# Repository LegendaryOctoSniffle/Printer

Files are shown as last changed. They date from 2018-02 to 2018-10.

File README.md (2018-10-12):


# Printer

Design is complete. It works:

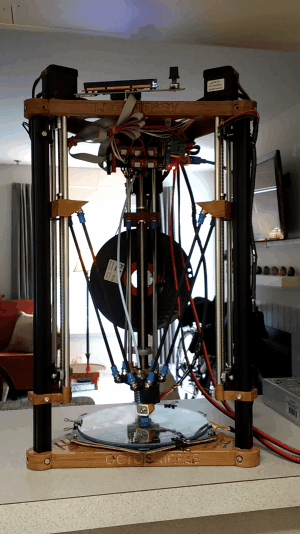
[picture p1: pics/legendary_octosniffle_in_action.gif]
the legendary octosniffle in action


This repository is for the LegendaryOctoSniffle design group. The LegendaryOctoSniffle will be a new 3D delta printer design, inspired by the RepRap [Kossel](http://reprap.org/wiki/Kossel) and [3DR](http://reprap.org/wiki/3DR). The printer will be designed around lead-screw drives and magnetic effector joints.

This repository will ultimately include models, images, instructions, parts lists, etc., for the construction of the LegendaryOctoSniffle. Presently, it contains coordinating instructions for the design group who will be creating these materials.

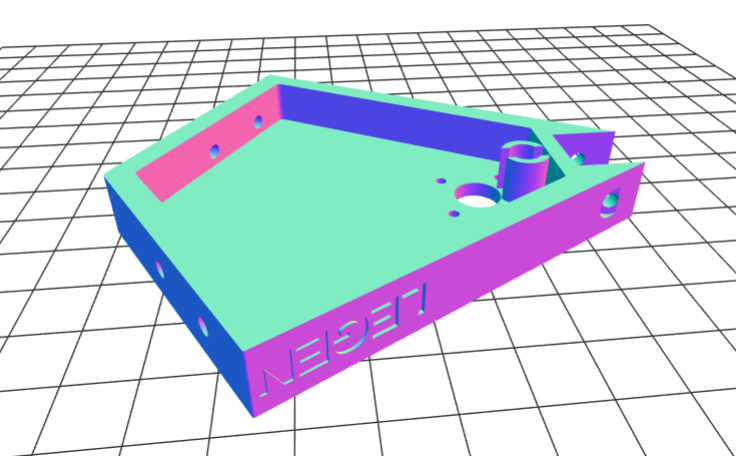
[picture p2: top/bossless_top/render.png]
Bossless top


## Goals

The primary design goals will be simplicity of assembly and simplicity of design: the LegendaryOctoSniffle will include a 3D printed structural top and base (inspired by the 3DR), magnetic effector joints, and a lead-screw drive. Aside from waiting for glue to dry, a practiced individual should be able to assemble the LegendaryOctoSniffle in one hour; a novice should be able to assemble it in less than four hours.

A secondary goal of the LegendaryOctoSniffle is to be a [RepRap machine](http://reprap.org/wiki/RepRap_Machines), like the Kossel, 3DR, and other machines that it is inspired by. The main requirement for this goal will be the licensing restrictions of any parts that the design group borrows from: GPL licensed parts will certainly be compatible with the RepRap project, and other licenses may also be suitable.

Another secondary goal of the printer is that it should be inexpensive. The basic build cost will be under $300.

## Audience

This repository currently supports the people who are designing the printer. It is anarchic, chaotic, and informal!

At some point, this repository might become a kind of reproducible design/learning experience for designing your own 3D printer.

## Structure

We will meet once a month for 4 or 5 months. The basic structure will be:

1. We'll buy some parts for the upcoming meeting.
2. We'll explore the function of those parts.
3. (Optional) We'll design the 3D printed parts necessary to assemble your purchased parts together. You can contribute to the design of these parts or just use other people's designs. Multiple people can independently design their own parts, working alone or together with others. And in the end, we don't have to settle on one "final" design: different people can use different solutions that they like best. Additionally, some parts can be taken directly from existing designs on the internet.
4. Send me your designs a week before the next meeting, and I'll have them printed for you. Or you can print them on your own if you have access to a 3D printer through a library, or work, etc.

## Schedule

### [Meeting 01: March 11th, 1:00PM, Study Room 5, Foster Business Library, University of Washington](meeting-01/)
### [Meeting 02: April 8th, 1:00PM-3:00PM, Suzallo Library Room 334, University of Washington](meeting-02/)
### [Meeting 03: July 7th. 1:00PM-3:00PM. University of Washington Campus (Suzallo 333)](meeting-03/)
### [Meeting 04: August 4th. 1:00PM-4:00PM. Radius Apartments rooftop common area (400 Boren Ave N, Seattle--SLU)](meeting-04/)

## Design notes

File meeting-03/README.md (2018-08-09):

# Meeting 03 - Saturday, July 7th. 1PM-3PM. University of Washington Campus (Suzzallo 333)

In this meeting, we will finish off the *structural* elements of our printer. In our next (and final) meeting, we will complete the *electrical* components of our printer.

## Parts

Here are the parts that you will need to purchase:

* 2020 Aluminum Extrusion (600mm) (x1)
  Yes, just one! [Ebay](https://www.ebay.com/itm/322880737350)
* T8x2 Leadscrew w/nut (500mm) (x2)
  Last time you bought 400mm. This time, buy two of the *500mm*. I'll swap you in third 500mm lead screw. Make sure that they are T8x2 screws. [Ebay](https://www.ebay.com/itm/322001200138?var=510950737978)
* Stepper Motor (Nema17, 1.7A) (x3)
  You have already bought one of these. Buy three more. You'll need two for the other two legs, and one for the extruder: the motor that pushes filament through the print head. [Ebay](https://www.ebay.com/itm/321966121485)
  
The quantities are weird because I'm making a shorter printer to fit on my counter, and I'll be giving you some of my longer parts. If you've already bought all three of your 2020 extrusions and lead screws, then that's not a problem!

## Pics from 7/7 meeting

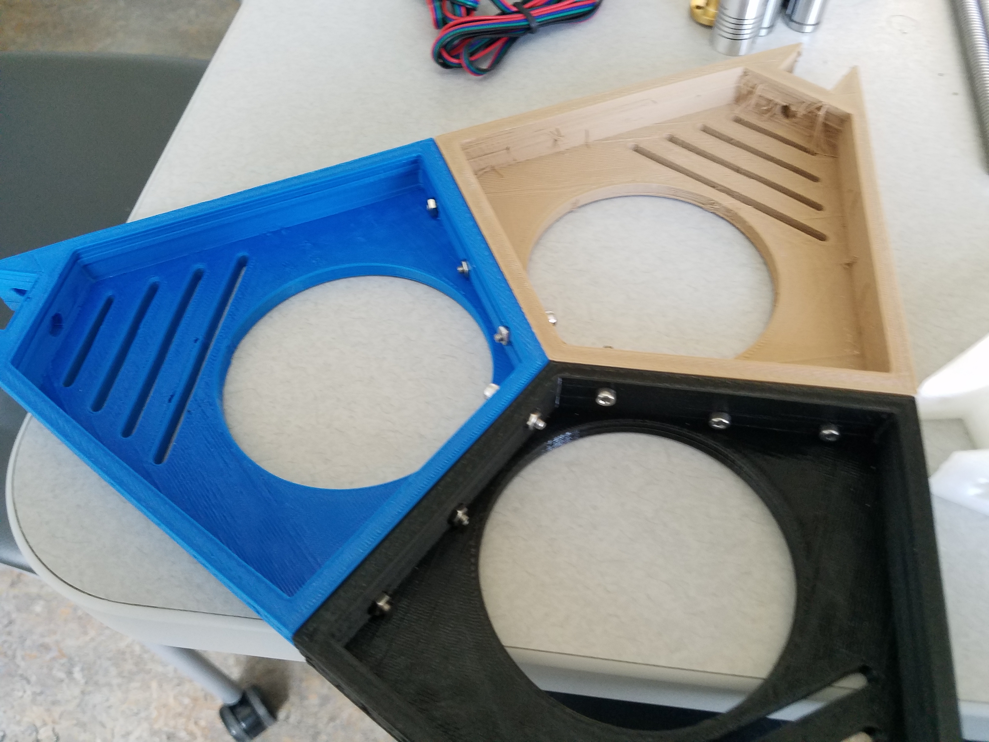
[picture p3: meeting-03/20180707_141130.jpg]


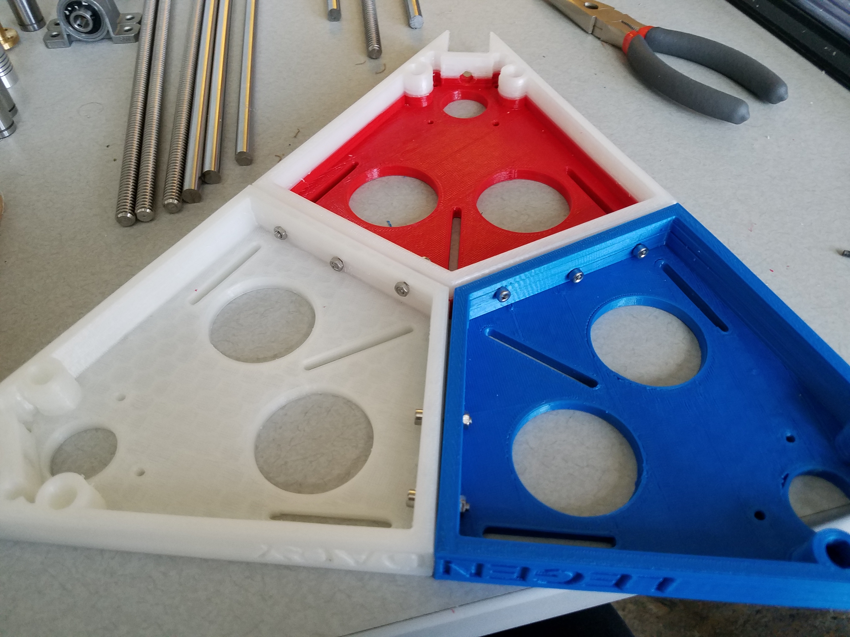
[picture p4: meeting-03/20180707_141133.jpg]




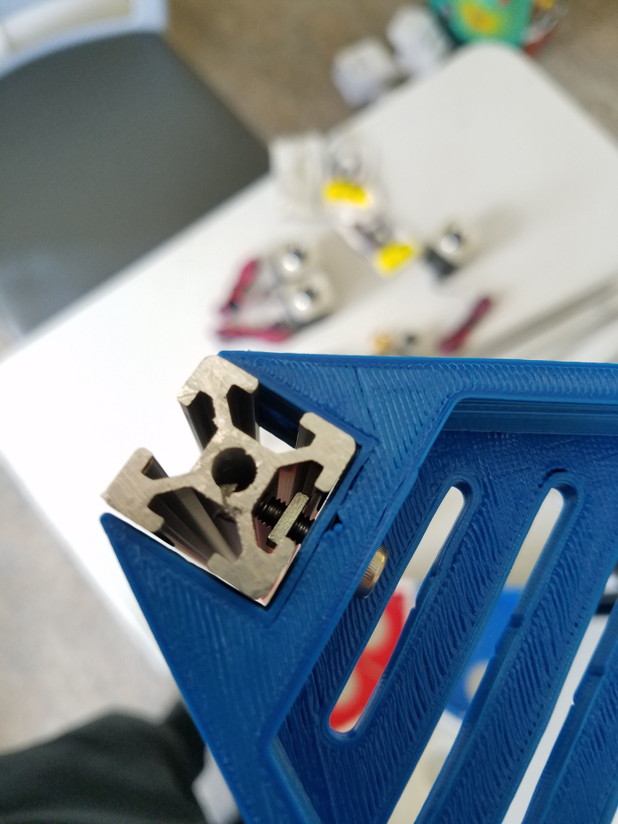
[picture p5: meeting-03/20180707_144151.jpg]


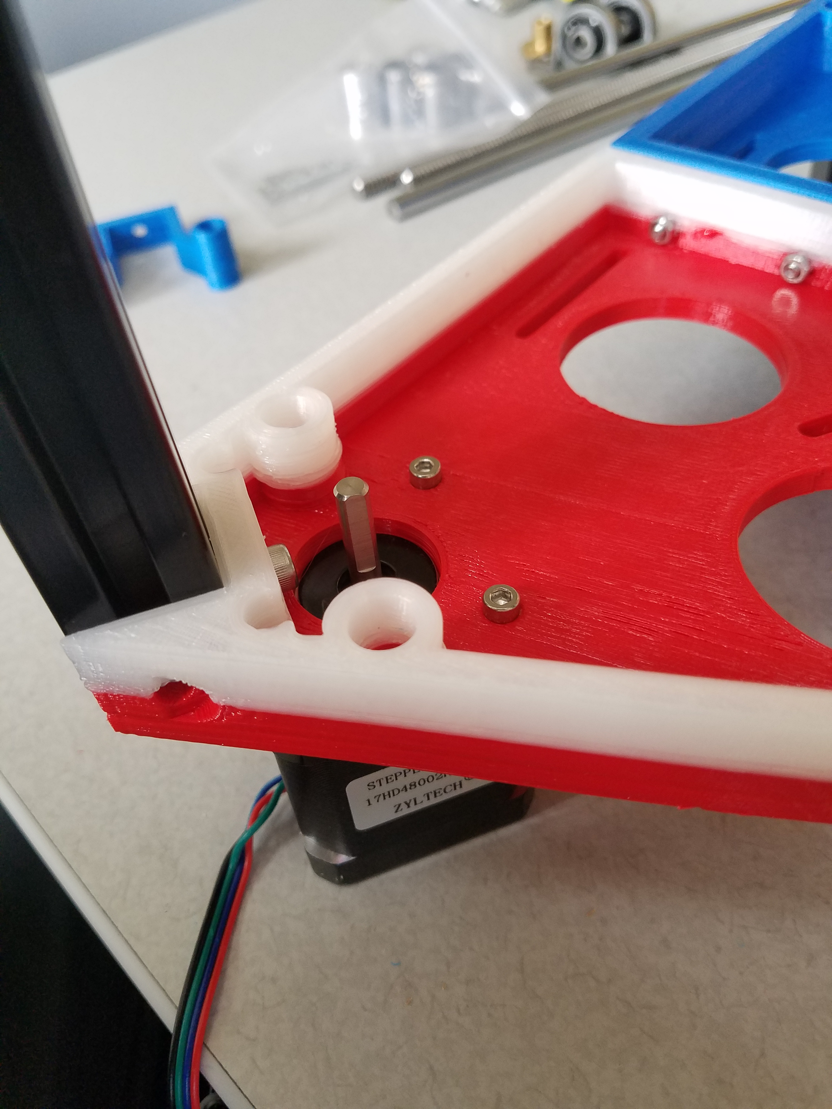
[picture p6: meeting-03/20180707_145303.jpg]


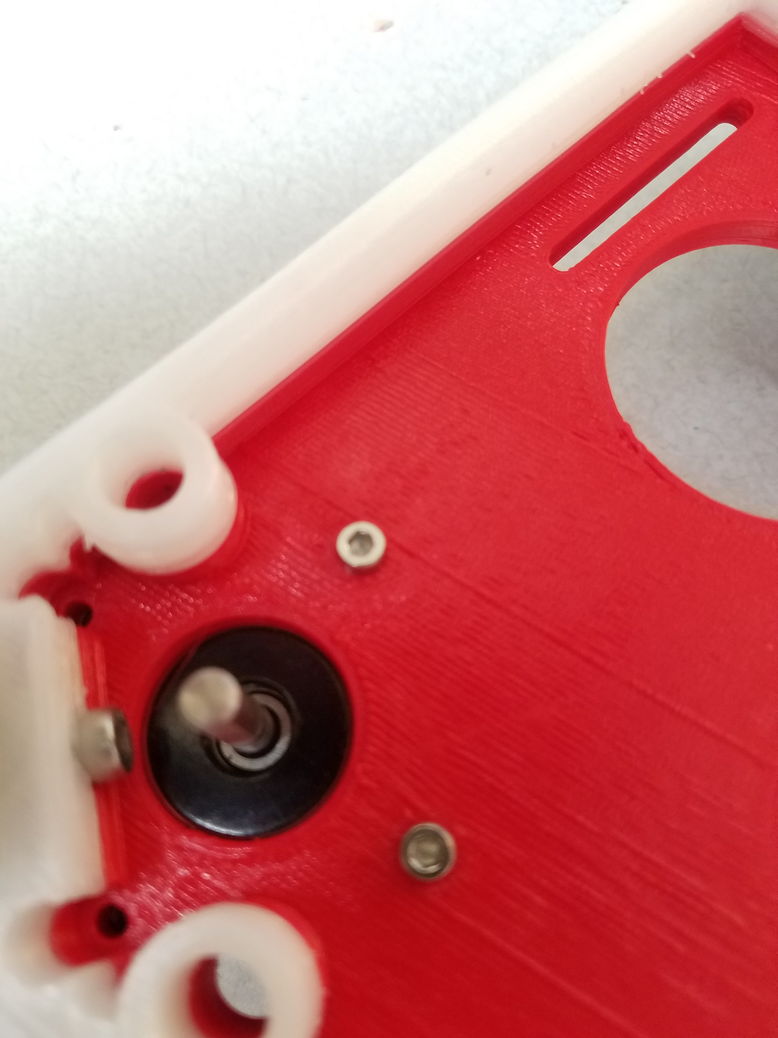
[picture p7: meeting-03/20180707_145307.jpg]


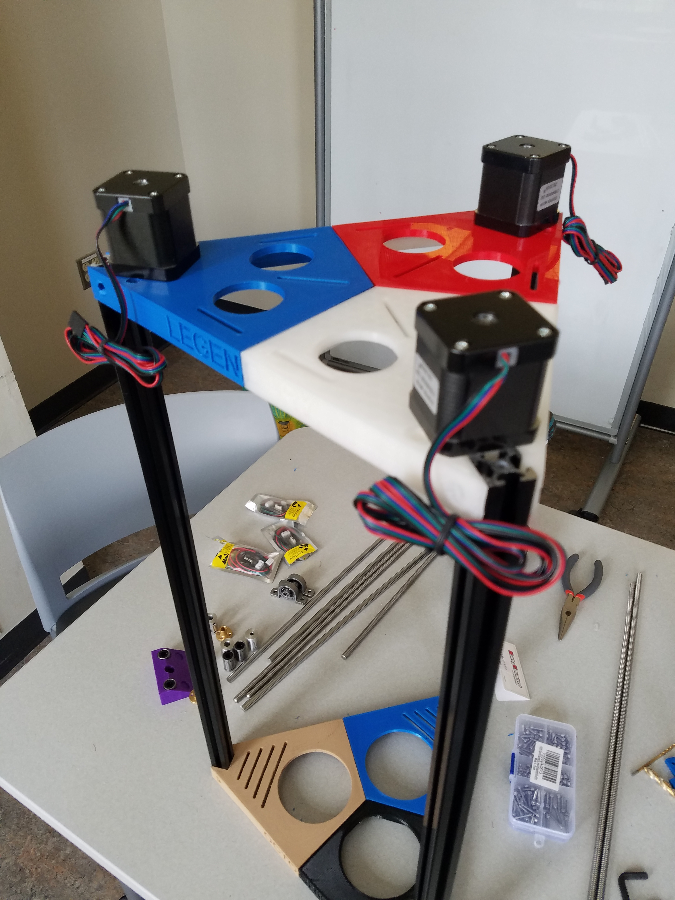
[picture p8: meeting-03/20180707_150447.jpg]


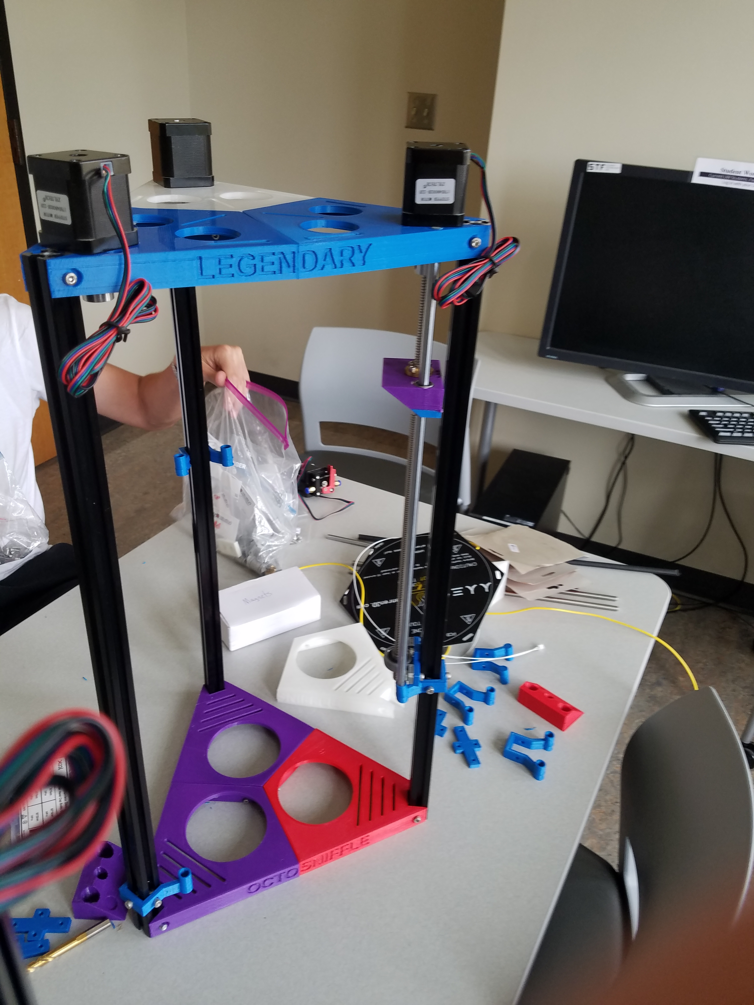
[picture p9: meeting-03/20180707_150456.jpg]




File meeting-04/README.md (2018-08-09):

# Meeting 04 - Saturday, August 4th. 1PM-4PM. Radius Apartments (Mike's building) __[rooftop common area](http://www.radiusslu.com/gallery/level-eight-amenities/)__: 400 Boren Ave N, Seattle, WA 98109 (South Lake Union) __[Map](https://goo.gl/maps/6jpcmqKH3d52)__

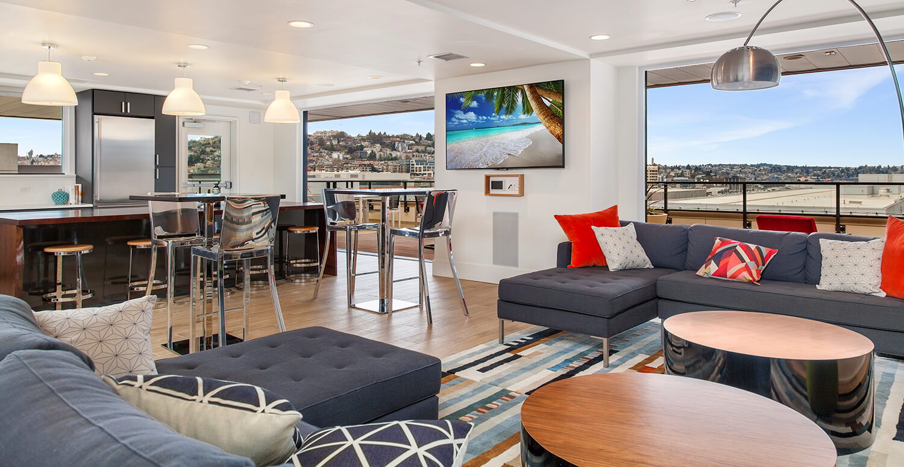
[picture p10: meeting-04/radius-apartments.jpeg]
Radius Apartments common area


In this (final) meeting, we will complete the *electrical* components of our printer. We're likely to use up all three hours calibrating our printers.

## Parts

* Power supply! 30 amps will be enough for a heated bed, plus dual extrusion (print two colors) if you decide to upgrade later. [Ebay](https://www.ebay.com/itm/Zyltech-12V-30A-360W-power-supply-PSU-for-3D-Printer-CNC-Arduino-Reprap-etc/322100961991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)
* Filament. Take your pick from [zyltech](https://www.ebay.com/sch/m.html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) on Ebay or on [Amazon](https://smile.amazon.com/s/ref=nb_sb_noss_2?url=search-alias%3Daps&field-keywords=PLA+1.75+filament). Get your color of choice, and anything with a decent rating will do. Don't get a specialty wood, metal, or fibre filament. It's important to get 1.75mm PLA. Get a full kilogram. Polylactic Acid (PLA) is plant-based, it has a fairly low melting temperature, and it doesn't shrink much as it cools.
* Control board! The RepRap Arduino Mega Pololu Shield (RAMPS) controller is based on an Arduino Mega 2560, with a 3D printer controlling "shield". Basically, we load a program onto the Arduino that has all of the logic of controlling the printer, and the Arduino talks to a second card which has all of the hardware for interfacing with the motors and heating elements. [ebay](https://www.ebay.com/itm/RAMPS-1-4-3D-PRINTER-CONTROLLER-Mega-2560-Atmega16u2-5x-A4988-2A-Drivers-More/321974766842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)
* LCD Controller. This LCD display includes an SD card reader and a wheel/button that lets you control the printer without attacking your computer. [ebay](https://www.ebay.com/itm/RAMPS-1-4-3D-PRINTER-2004-LCD-Smart-Controller/322017450535) Or if you wanted to be really cool, you could spring for this high(er) definition LCD: [ebay](https://www.ebay.com/itm/Genuine-ZYLtech-RAMPS-1-4-3D-PRINTER-12864-LCD-smart-controller/322148400468)
* Hot end. This is the part that we heat up and push plastic through. There are several manufacturers of hot ends, but most of them make clones of E3D. The V6 is E3D's flagship hot end, and so most manufacturers clone that version. Consequently, most printers are designed to accomodate a "V6 style" hotend. As simple as they are, hotends are somewhat prone to failure, and so it's worth it to spend a few extra dollars to get a decent one. For our printer, we will also need a "Bowden" style setup, which refers to separating the hotend of the extruder from the motor that is pushing filament through it. I'd suggest buying from Zyltech. [ebay](https://www.ebay.com/itm/V6-Style-Hotend-1-75mm-Bowden-style-Extruder-Conversion-Kit/322658052164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)
* Cold end. The "cold end" of the extruder is the part that pushes the plastic filament into the hot end. Here is a suitable one: [ebay](https://www.ebay.com/itm/2017-MK8-All-metal-1-75mm-Remote-Extruder-Kit-For-3D-Printer-Makerbot-Reprap-EV/222577699638). Either the "right" or "left" direction is fine.
* Build plate. The printer has to print "on" to a surface. Although it's not strictly necessary, an ideal build plate is heated to help keep the print warm through the duration of the entire print: this helps keep it from warping. Delta printers use round build plates. I would recommend buying [this](http://a.co/3r2tx1Q) one: people have knocked off stars for various reasons, none of which actually matter too much for our printer.

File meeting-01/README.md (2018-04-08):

Thanks to Kayla 🤘 for taking pictures and video, throughout Joe's explanations on how we'll be constructing 🏗️ the printer legs.

# Meeting 01

#### [See pics/vid from this meetup](https://github.com/LegendaryOctoSniffle/Printer/tree/master/meeting-01)

## Before the Meeting

Go ahead and purchase your [initial parts for meeting 01](#parts). I've received mine, and I'm excited! You might not have to bring all of your parts every time, but for this one do bring all of the parts that you receive. I received mine within a week of my order, but if you haven't received all of them by March 11th it won't be a big problem.

I'll refer to [this video](https://youtu.be/KroO4_xwKcs) to explain some of the parts that we'll be buying. Some of the parts and mechanisms will be different, but the basics will be the same.

The goal for the first meeting will be to create a working sled drive, minus the 3D printed parts. In the video above, the sleds are the orange things moving up and down the square rails.

The printer in the video uses a belt drive: the sleds are attached to a belt which is turned by motors in the base of the printer. The printer that we're making won't be using a belt: it will use a heavy threaded rod that's specially designed for driving precision movements.

## Parts

For our first meeting, we'll be assembling one "leg" of our printer. Though the parts list below is sufficient for one leg of the printer, we'll eventually be ordering three of all of the quantities provided below.

* T8x2 Leadscrew w/nut (400mm) (x1)
  This will be the threaded rod that will move each of our sleds up and down. We'll couple the motor to one end, and secure the length of the rod with a bearing that lets it turn freely. The x2 doesn't mean to buy 2 (yet), it designates the number of threads on the rod. [Ebay](https://www.ebay.com/itm/322001200138?var=510932183194)
* 8mm pillow block bearing. (x2)
  These are the bearings that will keep the rod aligned in place while letting it turn freely. Buy two. [Ebay](https://www.ebay.com/itm/2X-8mm-pillow-block-Self-aligning-bearing-mounted-support-3D-printer-CNC-Reprap-/322008974125). The linked item is a 2 pack: you can buy just one two pack. [Alternate Ebay listing](https://www.ebay.com/itm/2pcs-KP08-P08-8mm-Diameter-Bore-Self-Aligning-Pillow-Block-Bearing-/132306260310): if the first listing sells out, you can buy also buy this from the seller of the LM8UU bearings.
* 2020 Aluminum Extrusion (600mm) (x1)
  A mainstay of 3D printer construction. You'll see why. We'll use these as the vertical supports for our printer, connecting its structural top and bottom. [Ebay](https://www.ebay.com/itm/322880737350)
* Stepper Motor (Nema17, 1.7A) (x1)
  Stepper motors are built for precise, strong movement. Nema is a common standard for sizing stepper motors, and there are various Nema sizes. Additionally, stepper motors are rated by amperage. We'll be using a 1.7A Nema17 motor. [Ebay](https://www.ebay.com/itm/321966121485)
* 5mm to 8mm shaft coupler (x1)
  These will couple the 5mm shaft of our drive motor to the 8mm leadscrew. [Ebay](https://www.ebay.com/itm/321966928277)
* Endstop Switch (x1)
  When the printer first turns on, it doesn't know how far up or down the sleds are on the rods. To find out, it moves the sleds all the way up the rods until they make contact with a switch. When the sleds make contact with the switch, the printer knows the exact position of the sled: it's at the top of its rod. [Ebay](http://r.ebay.com/yveNca) The linked item is a three pack: it's got all the endstop switches we'll need for all three legs of the printer.
* 8mm by 400mm guide rod (x1)
  To drive our sled up and down, we'll mount it to the turning lead screw. But in order to keep the sled from turning, we'll need a second rod to guide it. [Ebay](https://www.ebay.com/itm/322454805576). We won't be making any other purchases from this seller, so I would recommend buying all three now.
* LM8UU 8mm linear bearing (x1)
  For our sled to slide up and down the guide rod, we'll need to equip it with a linear bearing. [Ebay](https://www.ebay.com/itm/141843551594) The linked item is a four pack. We'll need three total for all three legs, so you'll get them all in this one purchase.
  
Most of the items that I've linked to are sold by Zyltech. We'll be making most of our subsequent purchases from Zyltech as well. Some of their items offer a combined shipping discount. If you want to take advantage of free shipping then you can order up to three of all of the items I've listed from Zyltech, unless it's already a multipack: we'll need them for the other two legs.

## Designing the Carriage

Below is a sketch for a very basic design of the carriage/sled.

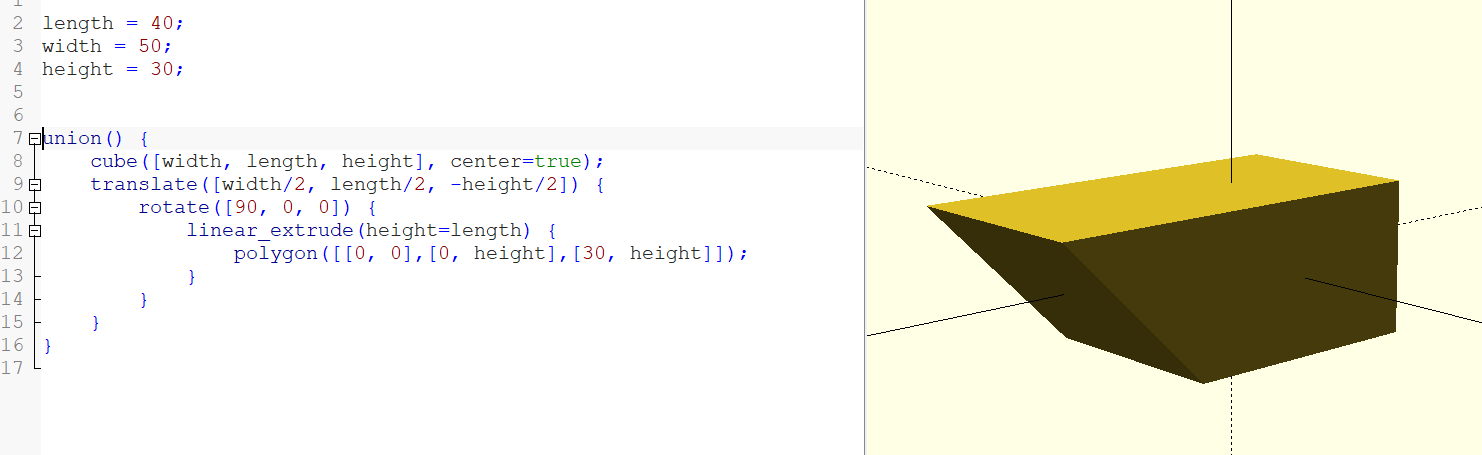
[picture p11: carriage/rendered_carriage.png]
Rendered example carraige


The sled has to:
  1. Hold on to the linear bearing (which slides up and down the smooth rod)
  2. Provide screw holes for the brass lead-screw nut and a hole for the lead-screw to go through.
  3. Have that 45 to 60 degree overhang.

If it fits that, it will do its job. I've provided an example SCAD with the basic shape, but it can be made taller or skinnier, or wider, etc. At the very least, you'll have to subtract out the holes. For example:
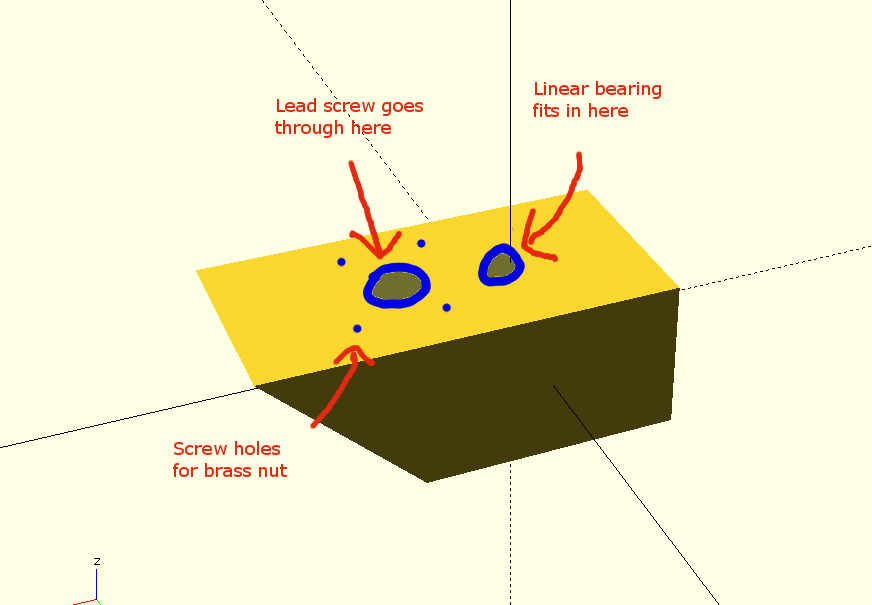
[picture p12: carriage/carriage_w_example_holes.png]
Rendered example carraige with holes

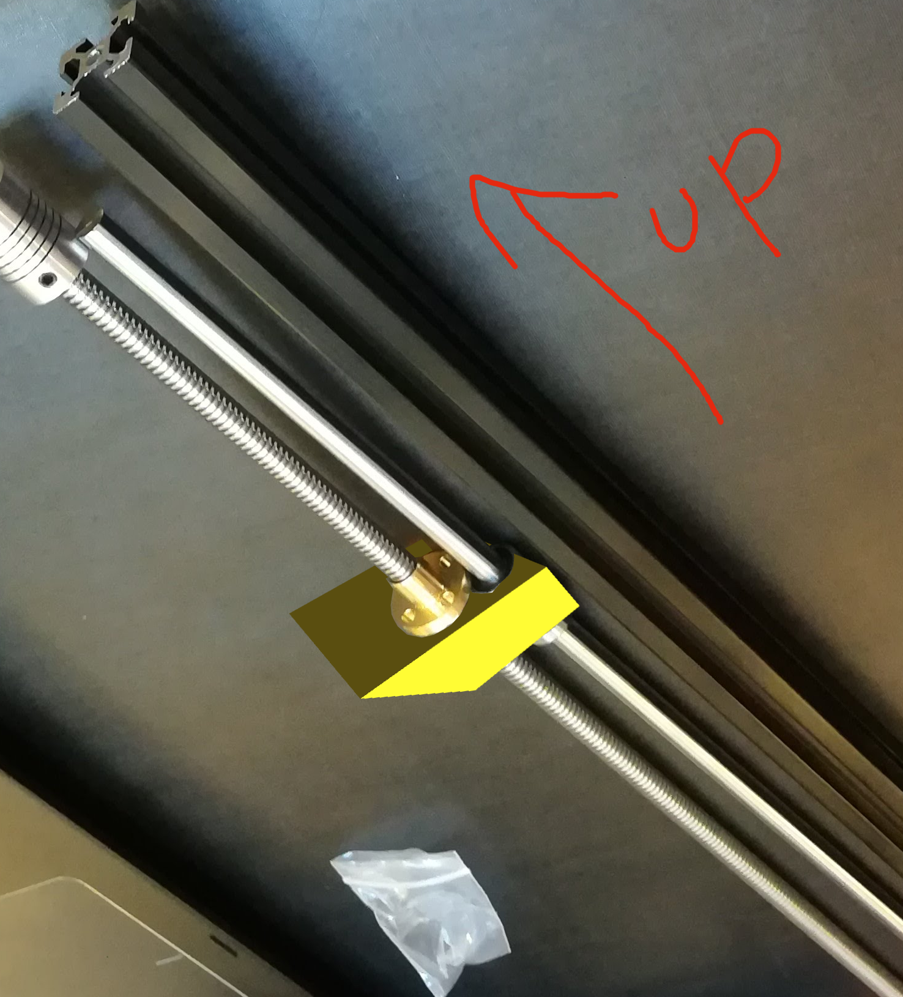
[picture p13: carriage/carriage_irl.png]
Carriage example in real life


Putting the two holes closer together is better than further apart, but they don't have to be too close together. Also, cool looking is better than not cool looking. And it's like 10 cents worth of plastic, so we can revise it once you see it printed and put together.

You can use a ruler to get the exact milimeter measurements of the parts, or you can guess. In any case, use variables as much as you can so that we can easily make changes.

For the screw holes, use a radius of 1mm.

I've also uploaded a SCAD with some example holes through it.
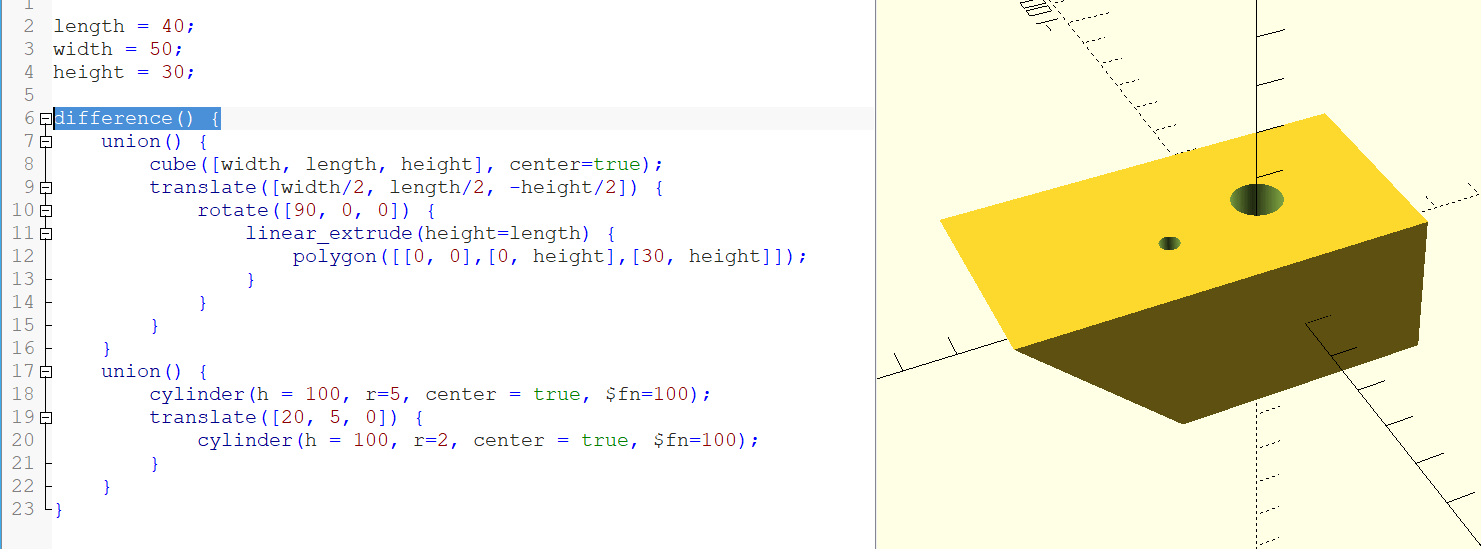
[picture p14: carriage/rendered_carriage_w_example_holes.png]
Carriage with example holes

See the SCAD itself for some helpful comments.

And the carriage SCADs are in the carriage directory.

### Problems Rendering in OpenSCAD?

Especially with Windows? I had [this problem](https://github.com/openscad/openscad/issues/1591), and resolved it with the "force Goldfeather" advice.

### Your Carriages

Push them into the /carriages directory! I'll print them a week before the next meetup.

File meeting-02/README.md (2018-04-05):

# April 8th Meetup, 1PM-3PM, Suzallo Room 334.
# Meeting 02

## Parts List

There will be no parts to buy.

## What To Bring

* (1) 2020 Aluminum Extrusion
* (1) Lead screw w/brass nut
* (1) Smooth rod w/linear bearing
* (1) Endstop switch
* (1) Pillow block bearing

## Outline

1. If you've designed a carriage/sled, then I'll print it and bring it! I'll print enough copies of at least one design for everyone to have one.
2. I'll bring some extra hardware (screws and tools) so that we can assemble the carriage, lead screw nut, and smooth rod.
3. I'll bring playdough, so that we can prototype the following parts:
  * Endstop switch setoff.
  * Pillow block bearing setoff.
  * Hardware to capture the smooth rod.
  * Structural top and base
4. I'll bring the effector joint magnets, and describe how they'll attach to the sled.

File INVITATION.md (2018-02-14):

# Invitation

Hey folks! I've had this idea rolling around in my head, and I'm ready to kick it off.

I'd like to put together a group to design a 3D printer. There are lots of home grown 3D printer designs out there. See for example http://reprap.org/wiki/RepRap_Machines. We'd mostly be selecting elements from existing printers to create a new combination, not developing any new technology. The goal I'd like to pursue is: few parts and ease of assembly/upgrade.

To throw a few words out there, it'll be a delta printer. That means it will look something like this: https://youtu.be/KroO4_xwKcs. It'll have a lead screw drive, with magnetic ball effector joints, and the structural base and top will be 3D printed. You'll know what all of that means later. (: Build cost will be less than $300.

I figure we'll meet once a month for four or five months. We'll start off with a small list of parts to buy, and add to it as we assemble the printer.

Though all of the technology is already out there, we will have to design some 3D printed parts. For that, there's a cool language called OpenSCAD. It's like 3D geometry meets Python, and easy to pick up. There are simple parts that we'll have to design, and also more complicated parts that we can either design or crib from other printers.

I'll bring sufficient experience with 3D printers: I've built a couple from kit so far. You can collaborate on the design of the printed parts, or just come and learn/assemble. Of course, I'll print all of the printed parts we need. I'll be doing this project with or without you, but of course it would be great to work together. (: I might rope in a few other friends.

I'm not sure how to best put a group together. But if you want to join, then star this repo (https://github.com/LegendaryOctoSniffle/Printer) ; I'll invite you to the group and figure out how to get in touch.

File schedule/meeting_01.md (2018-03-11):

# Meeting 01

Go ahead and purchase your [initial parts for March 11th](#parts). I've received mine, and I'm excited! You might not have to bring all of your parts every time, but for this one do bring all of the parts that you receive. I received mine within a week of my order, but if you haven't received all of them by March 11th it won't be a big problem.

I'll refer to [this video](https://youtu.be/KroO4_xwKcs) to explain some of the parts that we'll be buying. Some of the parts and mechanisms will be different, but the basics will be the same.

The goal for the first meeting will be to create a working sled drive, minus the 3D printed parts. In the video above, the sleds are the orange things moving up and down the square rails.

The printer in the video uses a belt drive: the sleds are attached to a belt which is turned by motors in the base of the printer. The printer that we're making won't be using a belt: it will use a heavy threaded rod that's specially designed for driving precision movements.

## Parts

For our first meeting, we'll be assembling one "leg" of our printer. Though the parts list below is sufficient for one leg of the printer, we'll eventually be ordering three of all of the quantities provided below.

* T8x2 Leadscrew w/nut (400mm) (x1)
  This will be the threaded rod that will move each of our sleds up and down. We'll couple the motor to one end, and secure the length of the rod with a bearing that lets it turn freely. The x2 doesn't mean to buy 2 (yet), it designates the number of threads on the rod. [Ebay](https://www.ebay.com/itm/322001200138?var=510932183194)
* 8mm pillow block bearing. (x2)
  These are the bearings that will keep the rod aligned in place while letting it turn freely. Buy two. [Ebay](https://www.ebay.com/itm/2X-8mm-pillow-block-Self-aligning-bearing-mounted-support-3D-printer-CNC-Reprap-/322008974125). The linked item is a 2 pack: you can buy just one two pack. [Alternate Ebay listing](https://www.ebay.com/itm/2pcs-KP08-P08-8mm-Diameter-Bore-Self-Aligning-Pillow-Block-Bearing-/132306260310): if the first listing sells out, you can buy also buy this from the seller of the LM8UU bearings.
* 2020 Aluminum Extrusion (600mm) (x1)
  A mainstay of 3D printer construction. You'll see why. We'll use these as the vertical supports for our printer, connecting its structural top and bottom. [Ebay](https://www.ebay.com/itm/322880737350)
* Stepper Motor (Nema17, 1.7A) (x1)
  Stepper motors are built for precise, strong movement. Nema is a common standard for sizing stepper motors, and there are various Nema sizes. Additionally, stepper motors are rated by amperage. We'll be using a 1.7A Nema17 motor. [Ebay](https://www.ebay.com/itm/321966121485)
* 5mm to 8mm shaft coupler (x1)
  These will couple the 5mm shaft of our drive motor to the 8mm leadscrew. [Ebay](https://www.ebay.com/itm/321966928277)
* Endstop Switch (x1)
  When the printer first turns on, it doesn't know how far up or down the sleds are on the rods. To find out, it moves the sleds all the way up the rods until they make contact with a switch. When the sleds make contact with the switch, the printer knows the exact position of the sled: it's at the top of its rod. [Ebay](http://r.ebay.com/yveNca) The linked item is a three pack: it's got all the endstop switches we'll need for all three legs of the printer.
* 8mm by 400mm guide rod (x1)
  To drive our sled up and down, we'll mount it to the turning lead screw. But in order to keep the sled from turning, we'll need a second rod to guide it. [Ebay](https://www.ebay.com/itm/322454805576). We won't be making any other purchases from this seller, so I would recommend buying all three now.
* LM8UU 8mm linear bearing (x1)
  For our sled to slide up and down the guide rod, we'll need to equip it with a linear bearing. [Ebay](https://www.ebay.com/itm/141843551594) The linked item is a four pack. We'll need three total for all three legs, so you'll get them all in this one purchase.
  
Most of the items that I've linked to are sold by Zyltech. We'll be making most of our subsequent purchases from Zyltech as well. Some of their items offer a combined shipping discount. If you want to take advantage of free shipping then you can order up to three of all of the items I've listed from Zyltech, unless it's already a multipack: we'll need them for the other two legs.

## Outline

* Review of project goals and methods
* Types of printers
  * Fused Deposition Modeling
  * Stereo Lithography
  * Laser Sintering
  * Additive vs. subtractive manufacturing
* Parts of the delta printer
  * Structural elements
    * Point out all the joints and how they're connected
  * Sleds/Carriages
    * Belt drive
    * Idler
    * Gear
    * Effector joints
    * Wheels
  * Stepper motor
    * What a stepper motor is
    * Difference from a servo
  * End stops
    * Absolute vs relative movement
    * Mention auto leveling
  * Effector
    * Effector arms and effector joints
    * The hot end
      * The hot end of the hot end
      * The cold end of the hot end
    * Single vs dual (or more!)
  * Extruder
    * The plastic tube
    * Bowden vs. direct drive
      * Weight
      * Elasticity, nozzle leak, and retraction
  * The computer
    * RAMPS vs...
    * Connects power, end stop switches, and motor control
    
* FDM printer geometries
  * Cartesian
    * [Video](https://www.youtube.com/watch?v=AomaNIpup30)
  * Delta
  * Complexity of software vs. complexity of assembly
  * Weird effects of delta printer math
* Printing a part
  * Selecting a model (stl)
  * Slicing
    * Brief overview of settings
  * The file that's generated
  * Transfering the file to the printer
* Our goal before the next session
  * Show 3DR printed top/bottom
  * Mock up assembly of parts, demonstrate lead screw drive
  * Comments on parameters for the computer software
  * Sled/carriage, with insets for effector joint magnets
    * Has to capture the lead screw nut
    * Has to capture linear bearing
  * Mount to hold the end stop switch
  * Mount to hold the pillow block bearing
  * Mount to hold the rod
* OpenSCAD basics
  * A cube
  * A cylinder
  * Translation
  * Rotation
  * Addition
  * Subtraction
  * The exclamation mark
  * Units
  * Don't worry about the floor
  * Don't worry about print rotation

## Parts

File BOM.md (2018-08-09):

Parts Group 1:

* T8x8 Leadscrew w/nut (500mm) (x3)
  This will be the threaded rod that will move each of our sleds up and down. We'll couple the motor to one end, and secure the length of the rod with a bearing that lets it turn freely. The x8 doesn't mean to buy 8, it designates the pitch of the rod threads. [Ebay](https://www.ebay.com/itm/T8x8-Lead-Screw-Pitch-2-Lead-8-Stainless-Rod-Linear-Rail-Bar-Shaft-w-Brass-Nut/372243139945)
* 8mm by 500mm guide rod (x6)
  To drive our sled up and down, we'll mount it to the turning lead screw. But in order to keep the sled from turning, we'll need a second rod to guide it. [Ebay](https://www.ebay.com/itm/8mm-CNC-3D-Printer-Axis-Chromed-Smooth-Rod-Steel-Linear-Rail-Shaft-300-400-500mm/192537955768).

Parts Group 2:

* 8mm pillow block bearing. (x3)
  These are the bearings that will keep the rod aligned in place while letting it turn freely. Buy three. [Ebay](https://www.ebay.com/itm/2X-8mm-pillow-block-Self-aligning-bearing-mounted-support-3D-printer-CNC-Reprap-/322008974125). The linked item is a 2 pack.
* 2020 Aluminum Extrusion (600mm) (x3)
  A mainstay of 3D printer construction. You'll see why. We'll use these as the vertical supports for our printer, connecting its structural top and bottom. [Ebay](https://www.ebay.com/itm/322880737350)
* Stepper Motor (Nema17, 1.7A) (x4)
  Stepper motors are built for precise, strong movement. Nema is a common standard for sizing stepper motors, and there are various Nema sizes. Additionally, stepper motors are rated by amperage. We'll be using a 1.7A Nema17 motor. [Ebay](https://www.ebay.com/itm/321966121485)
* 5mm to 8mm shaft coupler (x3)
  These will couple the 5mm shaft of our drive motor to the 8mm leadscrew. [Ebay](https://www.ebay.com/itm/321966928277)
* Endstop Switch (x3)
  When the printer first turns on, it doesn't know how far up or down the sleds are on the rods. To find out, it moves the sleds all the way up the rods until they make contact with a switch. When the sleds make contact with the switch, the printer knows the exact position of the sled: it's at the top of its rod. [Ebay](https://www.ebay.com/itm/3-PCS-Mechanical-Endstop-Switch-LED-RepRap-3D-Printer-Prusa-Mendel-RAMPS-1-4-CNC/321996978263) The linked item is a three pack.
* LM8UU 8mm linear bearing (x6)
  For our sled to slide up and down the guide rod, we'll need to equip it with a linear bearing. [Ebay](https://www.ebay.com/itm/141843551594) The linked item is a four pack.

Parts Group 3:

* Power supply! 30 amps will be enough for a heated bed, plus dual extrusion (print two colors) if you decide to upgrade later. [Ebay](https://www.ebay.com/itm/Zyltech-12V-30A-360W-power-supply-PSU-for-3D-Printer-CNC-Arduino-Reprap-etc/322100961991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)
* Filament. Take your pick from [zyltech](https://www.ebay.com/sch/m.html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) on Ebay or on [Amazon](https://smile.amazon.com/s/ref=nb_sb_noss_2?url=search-alias%3Daps&field-keywords=PLA+1.75+filament). Get your color of choice, and anything with a decent rating will do. Don't get a specialty wood, metal, or fibre filament. It's important to get 1.75mm PLA. Get a full kilogram. Polylactic Acid (PLA) is plant-based, it has a fairly low melting temperature, and it doesn't shrink much as it cools.
* Control board! The RepRap Arduino Mega Pololu Shield (RAMPS) controller is based on an Arduino Mega 2560, with a 3D printer controlling "shield". Basically, we load a program onto the Arduino that has all of the logic of controlling the printer, and the Arduino talks to a second card which has all of the hardware for interfacing with the motors and heating elements. [ebay](https://www.ebay.com/itm/RAMPS-1-4-3D-PRINTER-CONTROLLER-Mega-2560-Atmega16u2-5x-A4988-2A-Drivers-More/321974766842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)
* LCD Controller. This LCD display includes an SD card reader and a wheel/button that lets you control the printer without attacking your computer. [ebay](https://www.ebay.com/itm/RAMPS-1-4-3D-PRINTER-2004-LCD-Smart-Controller/322017450535) Or if you wanted to be really cool, you could spring for this high(er) definition LCD: [ebay](https://www.ebay.com/itm/Genuine-ZYLtech-RAMPS-1-4-3D-PRINTER-12864-LCD-smart-controller/322148400468)
* Hot end. This is the part that we heat up and push plastic through. There are several manufacturers of hot ends, but most of them make clones of E3D. The V6 is E3D's flagship hot end, and so most manufacturers clone that version. Consequently, most printers are designed to accomodate a "V6 style" hotend. As simple as they are, hotends are somewhat prone to failure, and so it's worth it to spend a few extra dollars to get a decent one. For our printer, we will also need a "Bowden" style setup, which refers to separating the hotend of the extruder from the motor that is pushing filament through it. I'd suggest buying from Zyltech. [ebay](https://www.ebay.com/itm/V6-Style-Hotend-1-75mm-Bowden-style-Extruder-Conversion-Kit/322658052164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)
* Cold end. The "cold end" of the extruder is the part that pushes the plastic filament into the hot end. Here is a suitable one: [ebay](https://www.ebay.com/itm/US-MK8-All-metal-1-75mm-Remote-Extruder-Kit-For-3D-Printer-Makerbot-Reprap/371731762554). Either the "right" or "left" direction is fine.
* Build plate. The printer has to print "on" to a surface. Although it's not strictly necessary, an ideal build plate is heated to help keep the print warm through the duration of the entire print: this helps keep it from warping. Delta printers use round build plates. I would recommend buying [this](http://a.co/3r2tx1Q) one: people have knocked off stars for various reasons, none of which actually matter too much for our printer.

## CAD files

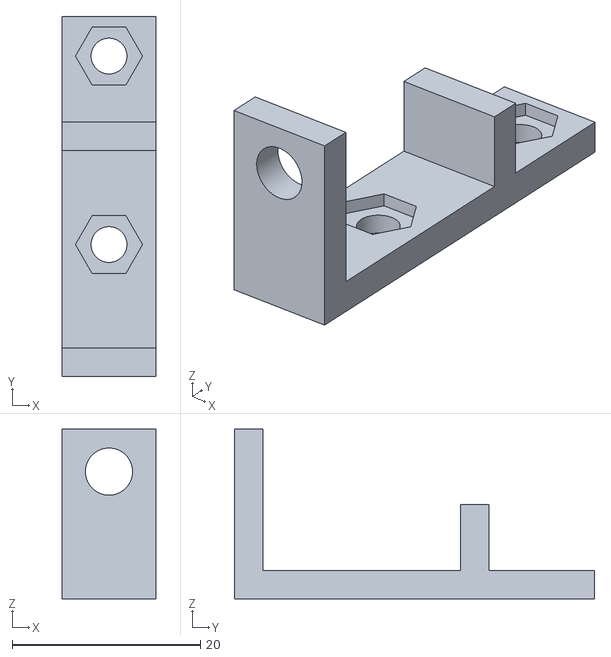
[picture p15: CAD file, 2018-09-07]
accessories/endstop_switch_mount/endstop_switch_mount.stl
10.0 x 38.2 x 18.0

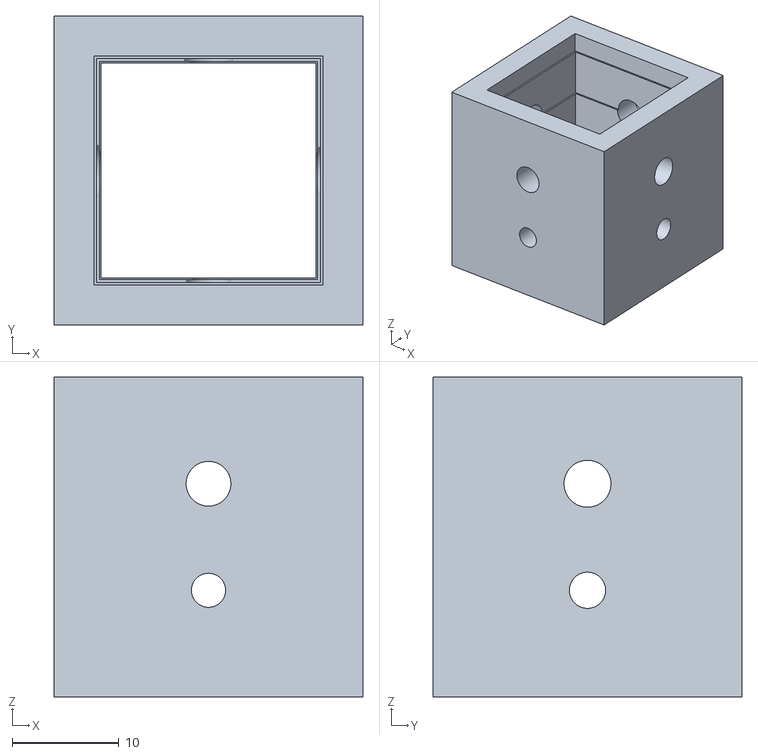
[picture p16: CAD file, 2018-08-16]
accuracy_test/accuracy_test.stl
29.0 x 29.0 x 30.0

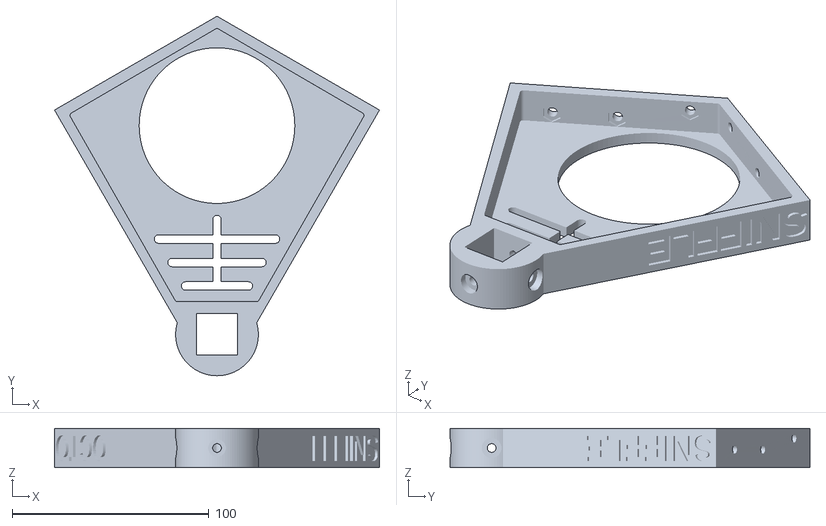
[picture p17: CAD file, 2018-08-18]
bottom/bossless_bottom/bossless_bottom.stl
165.0 x 182.5 x 20.0

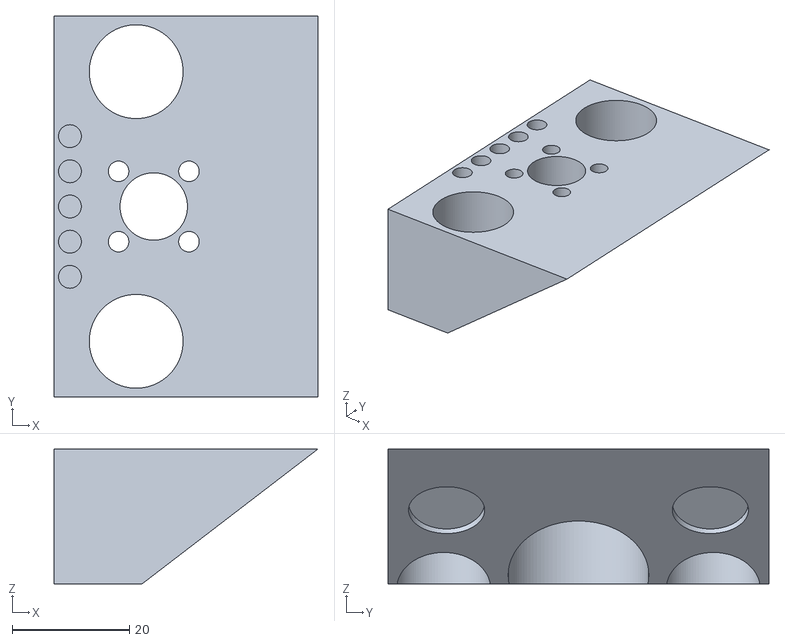
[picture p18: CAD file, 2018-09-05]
carriage/simple_carriage/simple_carriage.stl
45.0 x 65.0 x 23.0

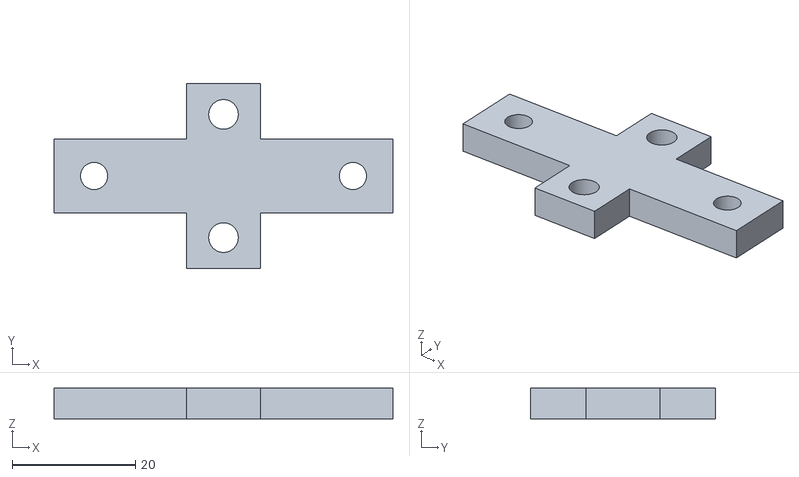
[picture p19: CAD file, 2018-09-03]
pillow_block_bearing_mount/pillow_block_bearing_mount.stl
55.0 x 30.0 x 5.00

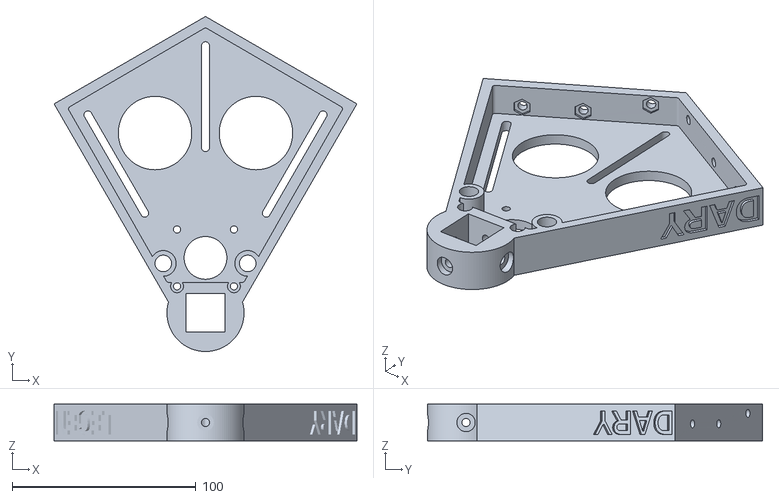
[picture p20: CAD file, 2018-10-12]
top/bossless_top/bossless_top.stl
165.0 x 182.5 x 20.0

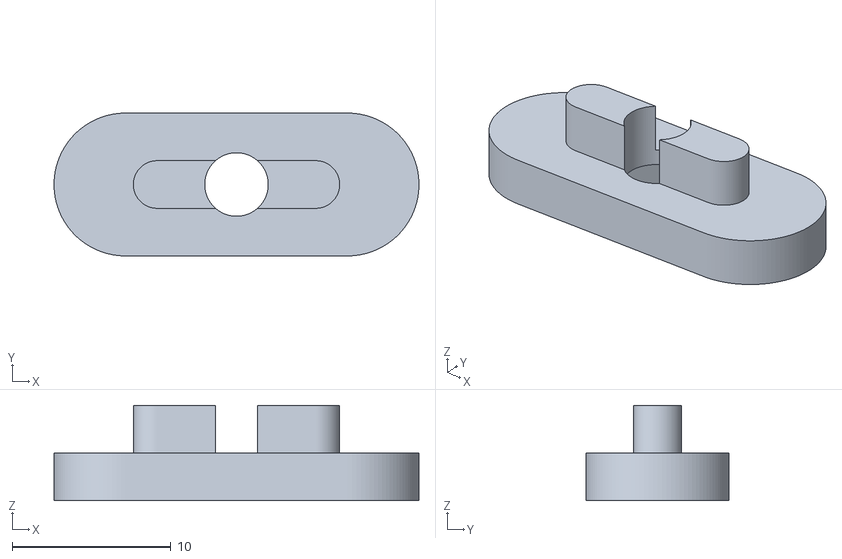
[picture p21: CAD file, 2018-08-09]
accessories/accessory_rail_nut_trap/accessory_rail_nut_trap.stl
23.0 x 9.00 x 6.00

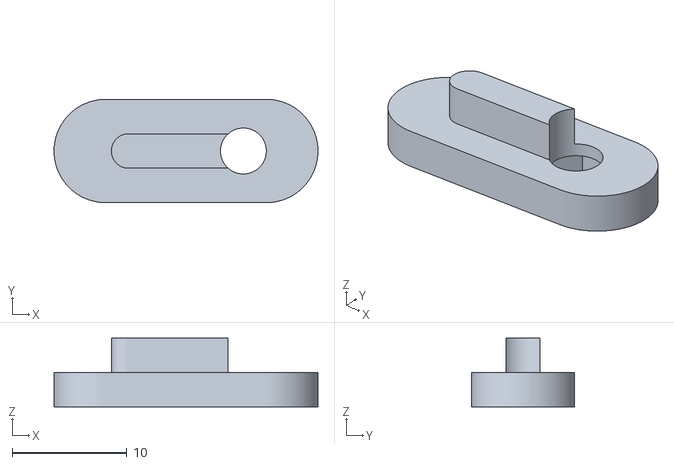
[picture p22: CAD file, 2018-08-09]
accessories/accessory_rail_nut_trap/side_accessory_rail_nut_trap.stl
23.0 x 9.00 x 6.00

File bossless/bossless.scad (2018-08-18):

function bossless_x(side_length) = cos(60) * side_length / 2;
function bossless_y(side_length) = sin(60) * side_length / 2;
function bossless_R(side_length) = side_length * sqrt(3) / 3;

module bossless(
    side_length,
    text_1="",
    text_2="",
    thickness=20,
    bottom_thickness=5,
    extrusion_inset=29,
    font_size_factor=2/3,
    extrusion_width=21,
    connection_screw_size=4.4,
    mounting_screw_size=4.4,
    mount_depth=5,
  ) {
  difference() {

    // The main bulk of the body
    linear_extrude(height = thickness) {
      polygon(points = [
        [-bossless_x(side_length)*.1, bossless_y(side_length)*.1],
        [bossless_x(side_length)*.1, bossless_y(side_length)*.1],
        [bossless_x(side_length) * 2, bossless_y(side_length) * 2],
        [-bossless_x(side_length) * 2, bossless_y(side_length) * 2]
      ]);
        
      translate([0, extrusion_inset, 0]) circle(d=42, $fn=100);

    }

    // Subtracting the other thirds of the triangle
    translate([0, 0, -.1 / 2])
    linear_extrude(height = thickness + .1) {
      polygon(
        points = [
          [-bossless_x(side_length) * 2 - .1, bossless_y(side_length) * 2],
          [bossless_x(side_length) * 2 + .1, bossless_y(side_length) * 2],
          [bossless_x(side_length), bossless_y(side_length)],
          [0, bossless_R(side_length)],
          [-bossless_x(side_length), bossless_y(side_length)],
        ]
      );

    }

    // Subtracting the extrusion
    translate([0, -extrusion_width/2 + extrusion_inset + extrusion_width / 2, 0]) {
      cube(size = [extrusion_width, extrusion_width, 50], center = true);
    }

    // Subtracting the screw to the left and right of the extrusion
    translate([0, extrusion_inset, thickness / 2]) {
      rotate([90, 0, 90]) {
        cylinder(d = mounting_screw_size, h = 100, center = true, $fn = 100);
        translate([0, 0, 50 + extrusion_width / 2 + mount_depth]) {
          cylinder(d = 10, h = 100, center = true, $fn = 100);
        }
        translate([0, 0, -(50 + extrusion_width / 2 + mount_depth)]) {
          cylinder(d = 10, h = 100, center = true, $fn = 100);
        }
      }
    }

    // Subtracting the screw to the front and back of the extrusion
    translate([0, extrusion_inset, thickness / 2]) {
      rotate([90, 0, 0]) {
        cylinder(d = mounting_screw_size, h = 100, center = true, $fn = 100);
        translate([0, 0, -(30/2 + extrusion_width/2 + mount_depth)]) {
          cylinder(d = 9, h = 30, center = true, $fn = 100);
        }
        translate([0, 0, 30/2 + extrusion_width/2 + mount_depth]) {
          cylinder(d = 9, h = 30, center = true, $fn = 100);
        }
      }
    }


    // Subtracting the "hollow center" of the main bulk
    translate([0, 0, bottom_thickness]) {
      linear_extrude(height = thickness) {
        hull() {
          translate([0, bossless_R(side_length) - side_length / 42.5, 0]) {
            circle(d = 3, center = true, $fn = 100);
          }
          translate([bossless_x(side_length) - side_length / 35, bossless_y(side_length) - side_length / 120, 0]) {
            circle(d = 3, center = true, $fn = 100);
          }
          translate([bossless_x(side_length) / 2.8 - side_length / 35, bossless_y(side_length) / 2.8 - side_length / 85, 0]) {
            circle(d = 3, center = true, $fn = 100);
          }
          translate([-(bossless_x(side_length) - side_length / 35), bossless_y(side_length) - side_length / 120, 0]) {
            circle(d = 3, center = true, $fn = 100);
          }
          translate([-(bossless_x(side_length) / 2.8 - side_length / 35), bossless_y(side_length) / 2.8 - side_length / 85, 0]) {
            circle(d = 3, center = true, $fn = 100);
          }
        }
      }
    }

    // Subtracting the screw holes that connect the three "tops"
    for (placement = [[1/5, bottom_thickness + 4.3], [1/2, bottom_thickness + 4.3], [15/18, thickness - 5]]) {
      screw_extension = placement[0];
      screw_height = placement[1];
      for (side = [1, -1]) {
        translate([
          side * bossless_x(side_length) * (1 - screw_extension),
          bossless_y(side_length) * (1 - screw_extension) + bossless_R(side_length) * (screw_extension),
          screw_height
        ]) {
          rotate([90, 0, -30 * side]) {
            cylinder(d = connection_screw_size, h = 20, $fn = 100, center = true);
          }
          if (side == -1) {
            rotate([90, 30, -30 * side]) {
              translate([0, 0, 7])
              cylinder(d = connection_screw_size*1.65 / cos(180 / 6) + 0.2, h = 5.5, $fn = 6, center = true);
            }
          }

        }
      }
    }

    // Subtracting text_1
    translate([-bossless_x(side_length), bossless_y(side_length), thickness / 2]) {
      rotate([90, 180, -60]) {
        translate([-1, 0, -1.5])
        linear_extrude(height = 8) {
          text(text_1, size=thickness*font_size_factor, font = "Helvetica:style=Bold", valign = "center", halign = "right");
        }
      }
    }

    // Subtracting t
    translate([bossless_x(side_length), bossless_y(side_length), thickness / 2]) {
      rotate([90, 180, 60]) {
        translate([.8, 0, -1.5])
        linear_extrude(height = 8) {
          text(text_2, size=thickness*font_size_factor, font = "Helvetica:style=Bold", valign = "center", halign = "left");
        }
      }
    }

  }
} // END MODULE

// Uncomment to test design:
// bossless(330);

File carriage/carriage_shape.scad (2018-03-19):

length = 40;
width = 50;
height = 30;


union() {
    cube([width, length, height], center=true);
    translate([width/2, length/2, -height/2]) {
        rotate([90, 0, 0]) {
            linear_extrude(height=length) {
                polygon([[0, 0],[0, height],[30, height]]);
            }
        }
    }
}

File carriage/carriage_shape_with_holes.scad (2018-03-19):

length = 40;
width = 50;
height = 30;

// The `difference` function subtracts the second thing from the first thing.
difference() {
    // Here's the basic shape. Union makes the multiple shapes into a single thing.
    union() {
        cube([width, length, height], center=true);
        translate([width/2, length/2, -height/2]) {
            rotate([90, 0, 0]) {
                linear_extrude(height=length) {
                    polygon([[0, 0],[0, height],[30, height]]);
                }
            }
        }
    }
    // Here are the cylinders that we're subtracting from the carriage.
    // I've unioned them together so that together they're the second
    // argument to the `difference` function.
    union() {
        // The $fn=100 is what makes this a nice smooth cylinder instead
        // of blocky garbage.
        cylinder(h = 100, r=5, center = true, $fn=100);
        translate([20, 5, 0]) {
            cylinder(h = 100, r=2, center = true, $fn=100);
        }
    }
}

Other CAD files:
pillow_block_bearing_mount/pillow_block_bearing_mount.scad
accessories/accessory_rail_nut_trap/accessory_rail_nut_trap.scad
accessories/endstop_switch_mount/endstop_switch_mount.scad
accuracy_test/accuracy_test.scad
bottom/bossless_bottom/bossless_bottom.scad
carriage/simple_carriage/simple_carriage.scad
example_scads/parametric_clamp.scad
top/bossless_top/bossless_top.scad

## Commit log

2018-03-14 Kayla's pics and video, documenting printer legs.
2018-03-19 Add example clamp scad.
    [parametric_clamp.scad]
2018-03-19 Add carriage documentation.
    [carriage_shape.scad, carriage_shape_with_holes.scad]
2018-04-05 Restructure repo.
    [carriage_shape.scad, carriage_shape_with_holes.scad]
2018-04-08 Add simple carriage.
    [simple_carriage.scad]
2018-04-12 Add bossless top.
    [bossless_top.scad, bossless_top.stl]
2018-05-21 Make top longer.
    [bossless_top.scad, bossless_top.stl]
2018-05-21 Adjust nut and screw width.
    [bossless_top.scad, bossless_top.stl]
2018-05-21 Move rods closer to edge.
    [bossless_top.scad, bossless_top.stl]
2018-05-21 Rotate nut traps.
    [bossless_top.stl]
2018-05-21 Add holes to route wires through.
    [bossless_top.scad, bossless_top.stl]
2018-05-21 Add some comments.
    [bossless_top.scad]
2018-05-21 Made M4 screw holes bigger.
    [bossless_top.scad, bossless_top.stl]
2018-05-21 Add bottom.
    [bossless_bottom.scad, bossless_bottom.stl]
2018-05-22 Couldn't triforce, but now I can.
    [bossless_top.scad, bossless_top.stl]
2018-05-22 Add accessory mounting rails.
    [bossless_top.scad, bossless_top.stl]
2018-05-22 Fix typo.
    [bossless_top.scad]
2018-05-23 Get text to pop in GitHub.
    [bossless_top.scad, bossless_top.stl]
2018-05-23 Make text show.
    [bossless_bottom.scad, bossless_bottom.stl]
2018-05-23 Update carriage to new offsets.
    [simple_carriage.scad, simple_carriage.stl]
2018-06-01 Refactor bossless_top to modules.
    [bossless.scad, bossless_top.scad, bossless_top.stl]
2018-06-01 Refactor bottom to modules.
    [bossless_bottom.scad, bossless_bottom.stl]
2018-06-01 Widen holes.
    [bossless_top.scad, bossless_top.stl]
2018-06-07 Expand hole for top screw.
    [bossless_top.scad, bossless_top.stl]
2018-06-07 Deeper nut traps.
    [bossless.scad]
2018-06-07 Apply deeper nut traps to top and bottom.
    [bossless_bottom.stl, bossless_top.stl]
2018-06-27 Add third screw hole.
    [bossless.scad]
2018-06-27 Adjustable font size.
    [bossless.scad]
2018-06-27 Use new bossless design for bottom.
    [bossless_bottom.scad, bossless_bottom.stl]
2018-06-27 Use new bossless design for top.
    [bossless_top.scad, bossless_top.stl]
2018-08-09 Add accessory rail nut trap.
    [accessory_rail_nut_trap.scad, accessory_rail_nut_trap.stl, side_accessory_rail_nut_trap.stl]
2018-08-09 Better whitespace and comments.
    [accessory_rail_nut_trap.scad, accessory_rail_nut_trap.stl]
2018-08-09 Consolidate BOM.
2018-08-09 Fix rod link.
2018-08-15 Add fourth screw mount.
    [bossless.scad]
2018-08-15 Variable screw size for piece connection.
    [bossless.scad]
2018-08-15 Remove legacy comments.
    [bossless.scad]
2018-08-16 Add accuracy test for printing.
    [accuracy_test.scad, accuracy_test.stl]
2018-08-18 Parameterize screw characteristics.
    [bossless.scad]
2018-08-18 Rebuild bottom with center accessory rail.
    [bossless_bottom.scad, bossless_bottom.stl]
2018-08-19 Rebuild for m4 screws.
    [bossless_top.scad, bossless_top.stl]
2018-08-19 Longer mounting rails.
    [bossless_top.scad, bossless_top.stl]
2018-09-03 Add pillow block bearing mount.
    [pillow_block_bearing_mount.scad, pillow_block_bearing_mount.stl]
2018-09-05 Parameterize simple carriage.
    [simple_carriage.scad]
2018-09-05 Mount flange under carriage.
    [simple_carriage.scad, simple_carriage.stl]
2018-09-07 Provide endstop switch mount.
    [endstop_switch_mount.scad, endstop_switch_mount.stl]
2018-10-12 Add action gif.
    [bossless_top.scad, bossless_top.stl, simple_carriage.scad]
